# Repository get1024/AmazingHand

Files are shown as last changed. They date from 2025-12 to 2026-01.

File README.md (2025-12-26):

Project is licensed under [Apache 2.0](https://www.apache.org/licenses/LICENSE-2.0)

Mechanical design is licensed under a:
[Creative Commons Attribution 4.0 International License][cc-by].
[][cc-by]
[][cc-by]

[cc-by]: http://creativecommons.org/licenses/by/4.0/
[cc-by-image]: https://licensebuttons.net/l/by/4.0/88x31.png
[cc-by-shield]: https://img.shields.io/badge/License-CC%20BY-lightgrey.svg

# Amazing Hand project

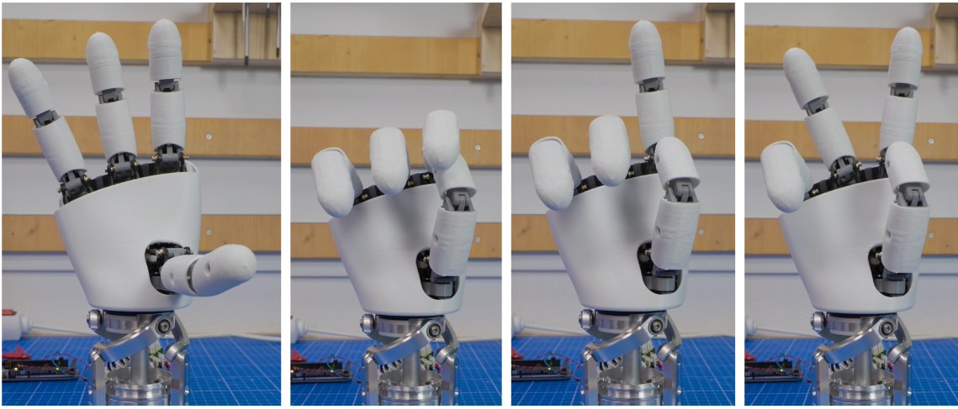
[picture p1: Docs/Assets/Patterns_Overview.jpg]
Patterns


Robotic hands are often very expensive and not so expressive. More dexterous ones often need cables and deported actuators in the forearm, i.e.,

The aim of this project is to be able to explore humanoid hand possibilities on a real robot (and Reachy2 is the perfect candidate for that !) with moderate cost.
=> Wrist interface is designed for Reachy2's wrist (Orbita 3D), but it can be easily adapted to other robot's wrist...

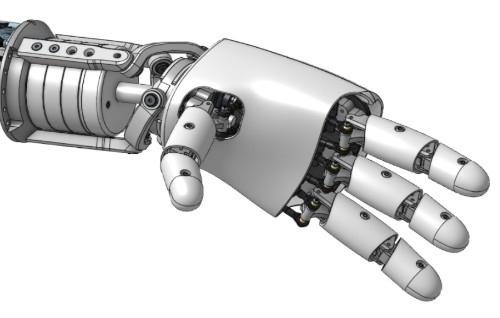
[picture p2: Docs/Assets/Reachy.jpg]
Reachy


Amazing Hand is:
- 8 dofs humanoid hand with 4 fingers
- 2 phalanxes per finger articulated together
- flexible shells almost everywhere
- All actuators inside the hand, without any cables
- 3D printable
- 400g weight
- low-cost (<200€)
- open-source

[AmazingHand_Overview](/docs/AmazingHand_Overview.pdf)

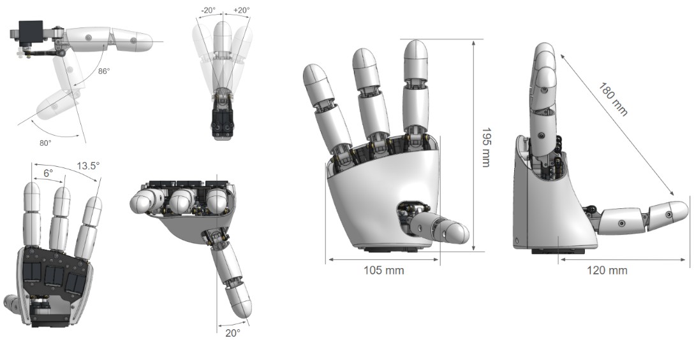
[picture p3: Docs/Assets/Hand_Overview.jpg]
Hand Overview

Each finger is driven by a parallel mechanism. 
That means 2x small Feetech SCS0009 servos are used to move each finger in flexion/extension and abduction/adduction

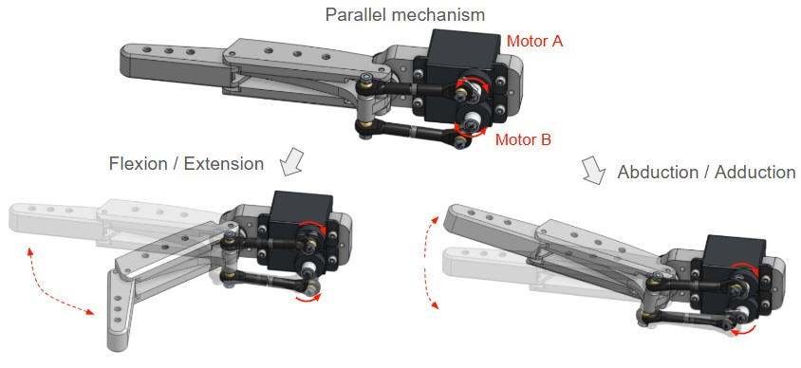
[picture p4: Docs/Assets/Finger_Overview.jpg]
Finger Overview


Two control methods are available:
- Use a serial bus driver (Waveshare i.e.) + Python script
- Use an Arduino + Feetech TTL Linker

Detailed explanations are available for both ways, and basic demo software is also available.
Up to you !

## Table of contents

- [Amazing Hand project](#amazing-hand-project)
  - [Table of contents](#table-of-contents)
- [Build Resources](#build-resources)
  - [BOM (Bill Of Materials)](#bom-bill-of-materials)
  - [CAD Files and Onshape document](#cad-files-and-onshape-document)
  - [Assembly Guide](#assembly-guide)
  - [Run basic Demo](#run-basic-demo)
  - [You need both right \& left hands on the same bus ?](#you-need-both-right--left-hands-on-the-same-bus-)
- [Disclaimer](#disclaimer)
- [AmazingHand advanced Demo](#amazinghand-advanced-demo)
- [Don't want to build it by yourself?](#dont-want-to-build-it-by-yourself)
- [Project Updates \& Community](#project-updates--community)
  - [Updates from community](#updates-from-community)
  - [To Do List](#to-do-list)
  - [FAQ](#faq)
  - [Contact](#contact)
  - [Thank you](#thank-you)

# Build Resources
## BOM (Bill Of Materials)
List of all needed components is available here:  
[AmazingHand BOM](https://docs.google.com/spreadsheets/d/1QH2ePseqXjAhkWdS9oBYAcHPrxaxkSRCgM_kOK0m52E/edit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)  
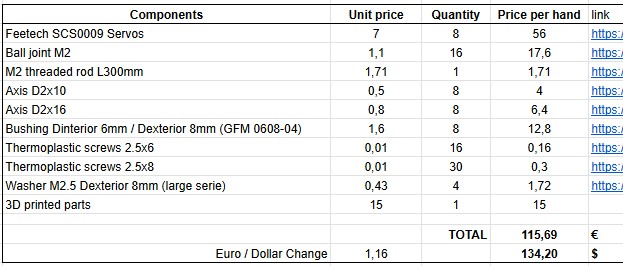
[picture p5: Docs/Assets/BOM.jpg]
BOM


And remember to add control choice cost (2 options detailed previously)

Details for custom 3D printed parts are here: 
[3Dprinted parts](https://docs.google.com/spreadsheets/d/1QH2ePseqXjAhkWdS9oBYAcHPrxaxkSRCgM_kOK0m52E/edit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)

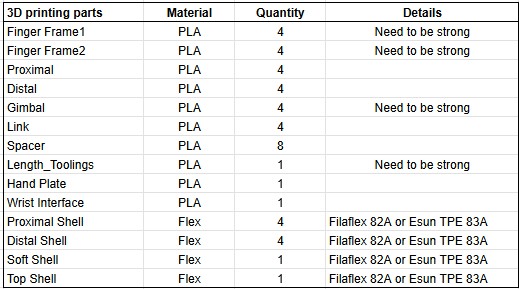
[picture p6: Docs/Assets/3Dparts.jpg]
3Dparts


Here is a guide explaining how to print all the needed custom parts:
[=> 3D Printing Guide](/docs/AmazingHand_3DprintingTips.pdf)
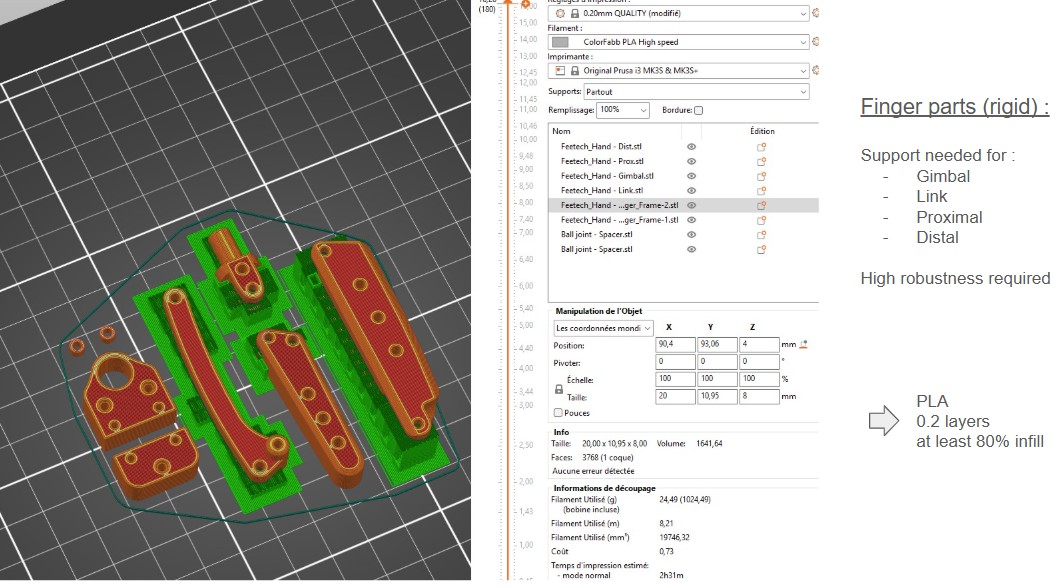
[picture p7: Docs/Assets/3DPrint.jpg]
3DPrint_example
 

## CAD Files and Onshape document
STL and Steps files can be found [here](https://github.com/pollen-robotics/AmazingHand/tree/main/cad) 

Note that fingers are the same if you want to build a left hand, but some parts are symmetrical. Specific right hand parts are preceded by an "R", and other left hand parts by an "L".

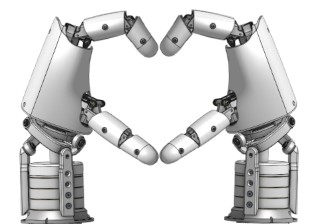
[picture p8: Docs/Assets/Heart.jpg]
Heart


Everyone can access the Onshape document too:   
[Link Onshape](https://cad.onshape.com/documents/430ff184cf3dd9557aaff2be/w/e3658b7152c139971d22c688/e/bd399bf1860732c6c6a2ee45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)  

Note that predefined positions are available in the "named position" tooling, with corresponding servo angles

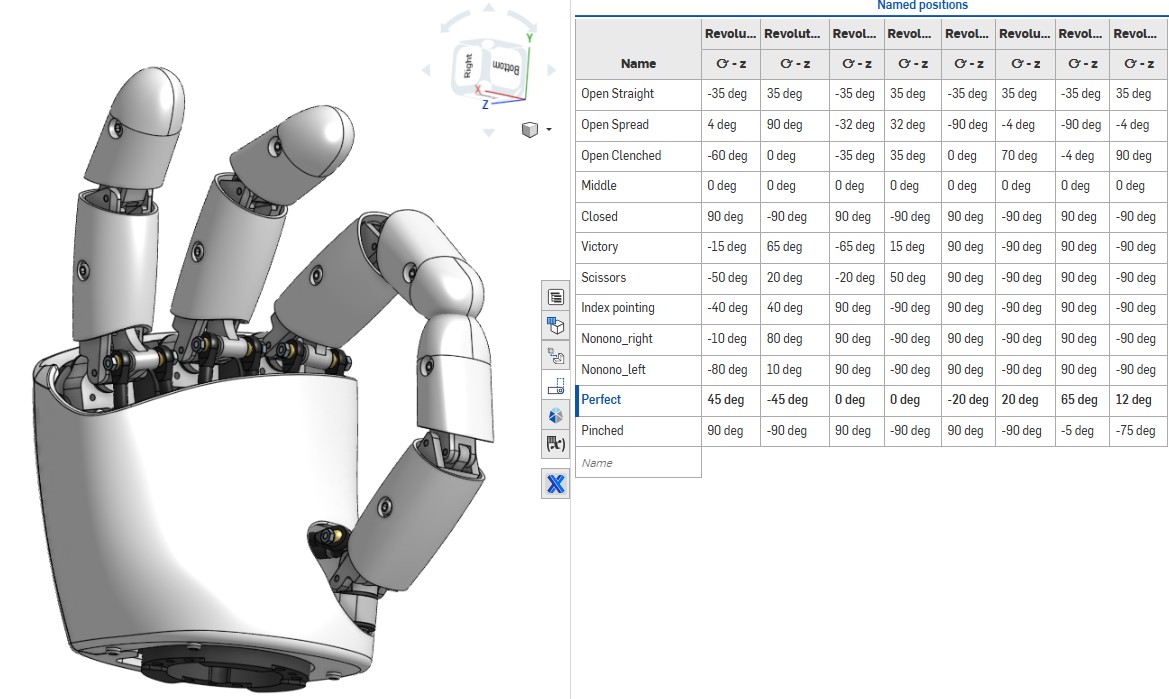
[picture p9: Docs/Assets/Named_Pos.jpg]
Onshape&Named_Pos
  

## Assembly Guide

Assembly guide for the Amazing Hand in combination with standard components in the BOM is here:  
[=> Assembly Guide](/docs/AmazingHand_Assembly.pdf)  
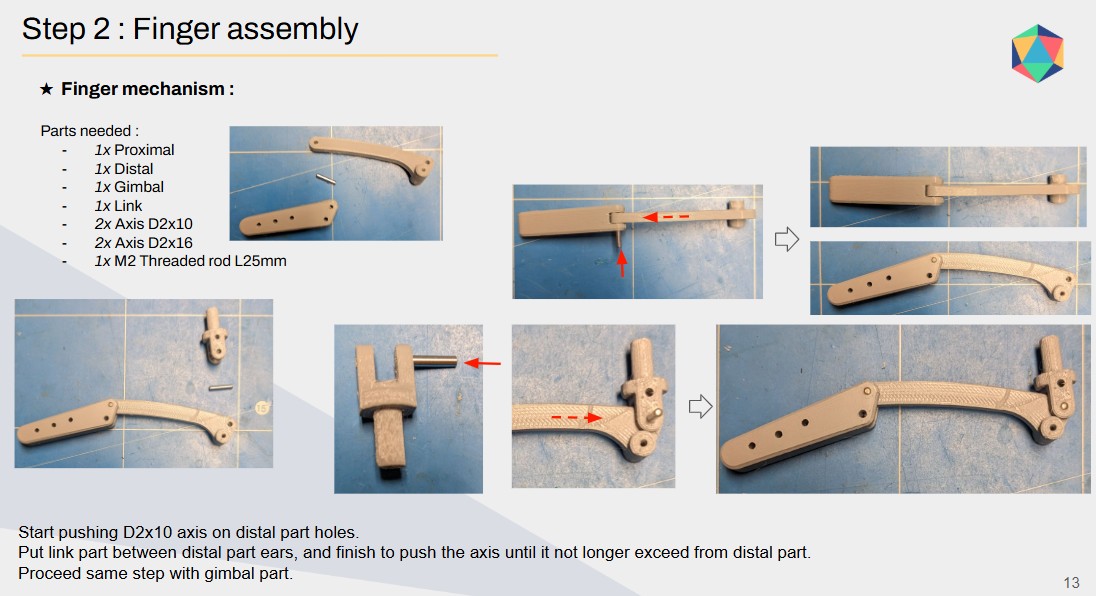
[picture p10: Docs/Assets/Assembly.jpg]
Assembly_example
  

You will need a simple program / script to calibrate each finger, available here:
- With Python & Waveshare serial bus driver: [here](https://github.com/pollen-robotics/AmazingHand/tree/main/PythonExample)
- With Arduino & TTLinker: [here](https://github.com/pollen-robotics/AmazingHand/tree/main/ArduinoExample)

Note that this assembly guide is for a standalone right hand.

If you need to build a standalone left hand, you can keep the same IDs for servo locations, and select if it's a right or left hand in the software.

## Run basic Demo

A basic demo is available with both Python & Arduino.

You will need an external power supply to be able to power the 8 actuators inside the hand.

If you don't have one already, a simple external power supply could be a DC/DC 220V -> 5V / 2A adapter with jack connector.
Check on the BOM list:
[AmazingHand BOM](https://docs.google.com/spreadsheets/d/1QH2ePseqXjAhkWdS9oBYAcHPrxaxkSRCgM_kOK0m52E/edit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) 

- Python script: "AmazingHand_Demo.py" [here](https://github.com/pollen-robotics/AmazingHand/tree/main/ArduinoExample)
  
- Arduino program: "AmazingHand_Demo.ino" [here](https://github.com/pollen-robotics/AmazingHand/tree/main/PythonExample)

https://github.com/user-attachments/Docs/Assets/485fc1f4-cc57-4e59-90b5-e84518b9fed0

## You need both right & left hands on the same bus ?

If you need to build both right and left hands to plug them on a robot, you will have to attribute different IDs for right and left hands. You can't have same ID for different servos on the same serial bus...
Very important thing is to keep same assembly order for servos, but set them different IDs than for the right hand, as follows:
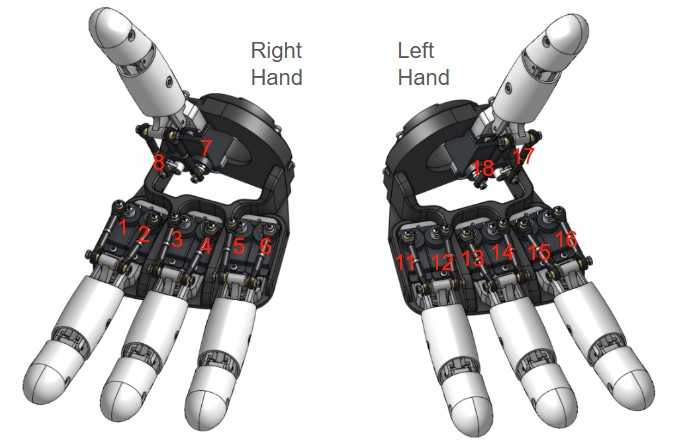
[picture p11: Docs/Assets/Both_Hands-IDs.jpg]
IDs


Specific software is also needed, in order to drive each hand independently.
This simple demo runs the same hand patterns on both hands simultaneously, but it's only available in Python:
"AmazingHand_Demo_Both" [here](https://github.com/pollen-robotics/AmazingHand/tree/main/PythonExample)

# Disclaimer

I noticed some variations between theoretical angles for Flexion / Extension, Abduction / Adduction and angles in real life prototypes. This is probably due to several sources of variation (3D printed parts are not perfect, balljoint rods are manually adjusted one by one, servo horn rework, flexibility of plastic parts...).

This design has not yet been tested for long and complex prehensile tasks. Before being able to grasp objects safely (that means without damaging servos or mechanical parts), a kind of smart software needs to be built.
SCS0009 servos have smart capabilities as:
- Torque enable / disable
- Torque feedback
- Current position sensor
- Heat temperature feedback
- ...

# AmazingHand advanced Demo
Tracking demo (https://www.youtube.com/watch?v=U0TfeG3ZUto)

For more advanced usage using inverse/forward kinematics there are several examples in the [Demo](Demo) directory along with some useful tools to test/configure the motors.

# Don't want to build it by yourself?
=> Kits are available here :

Seeed Studio :
https://www.seeedstudio.com/Amazing-Hand-Right-Hand-The-Open-Source-Robotic-Hand-Developer-Kit.html

WowRobo :
https://shop.wowrobo.com/products/amazing-hand-the-open-source-robotic-hand-kit

# Project Updates & Community
## Updates from community

- ### Amazing Base for the amazing hand : 
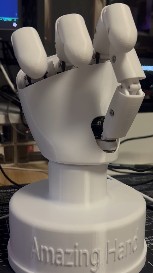
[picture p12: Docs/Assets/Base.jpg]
Base

STL or Step file can be found [here](https://github.com/pollen-robotics/AmazingHand/tree/main/cad) 

- ### Specific Chinese BOM available here :
[Chinese BOM](https://docs.google.com/spreadsheets/d/1fHZiTky79vyZwICj5UGP2c_RiuLLm89K8HrB3vpb2h4/edit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)

Thanks to Jianliang Shen !

- ### Amazing hand with SG90 servos + force control setup 🔥

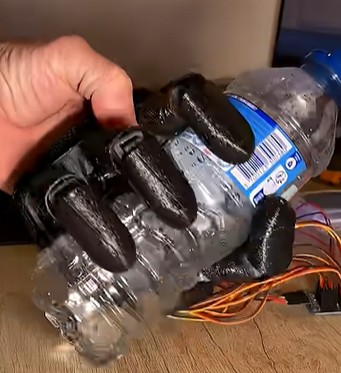
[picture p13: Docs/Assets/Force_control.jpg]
Force_control

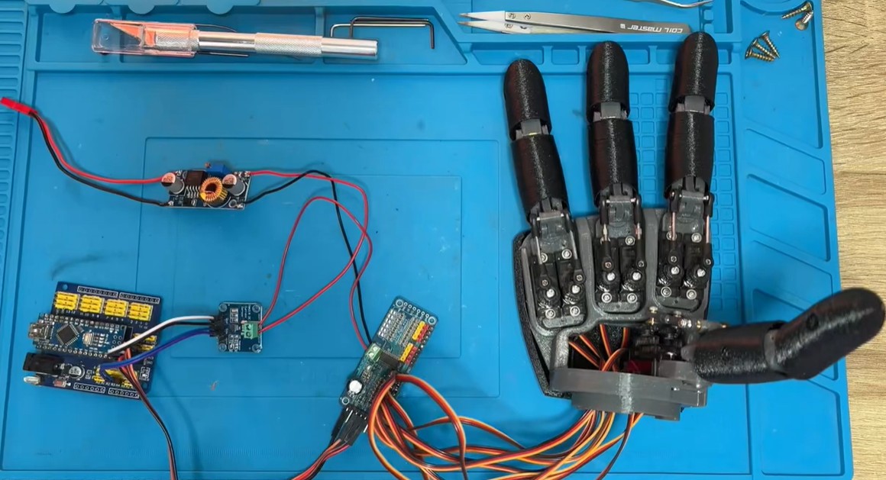
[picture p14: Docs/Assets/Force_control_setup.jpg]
Force_control_setup


GitHub with code: (https://github.com/joanbox24/AmazingHand-with-sg90-servo-force-control)

## To Do List
- Design small custom pcb with serial hub and power supply functions, to fit everything in the hand
- Test with prehensile tasks 
      => Add smarter behaviour for closing hand, based on available motors feedbacks
- Study possibility to have 4 different fingers length, or add a 5th finger
- Study possibility to use STS3032 Feetech motors instead of SCS0009
      => Stronger for quite the same volume, but servo horn is different
- Study possibility to add compliancy by replacing rigid links to springs
- Add fingertip sensor to push one step higher smart control

## FAQ
WIP

## Contact

You can reach public discord channel here : 
[Discord AmazingHand](https://discord.com/channels/519098054377340948/1395021147346698300)

Or 
[Contact me or Pollen Robotics](/docs/contact.md)

## Thank you
Huge thanks to those who have contributed to this project so far:
- [Steve N'Guyen](https://github.com/SteveNguyen) for beta testing, Feetech motors integration in Rustypot, Mujoco/Mink and hand tracking demo
- [Pierre Rouanet](https://github.com/pierre-rouanet) for Feetech motors integration in pypot  
- [Augustin Crampette](https://fr.linkedin.com/in/augustin-crampette) & [Matthieu Lapeyre](https://www.linkedin.com/in/matthieulapeyre/) for open discussions and mechanical advices

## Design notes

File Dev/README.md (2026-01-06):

# AmazingHand 控制实例教程

## 1. 知识大纲

`Dev` 目录包含以下核心组件：

*   **AHControl/**：基于 Rust 的驱动程序和机械手控制逻辑。
    *   `config/`：用于舵机映射和校准的 TOML 配置文件。
    *   `src/bin/`：用于舵机管理的实用二进制文件（`change_id`, `goto`, `get_zeros`, `set_zeros`）。
    *   `src/main.rs`：**Dora-rs** 管道的主控制节点。它读取 TOML 配置，监听来自仿真的关节位置更新（例如 `mj_r_joints_pos`），应用配置的偏移/反转，并同步写入舵机。
*   **AHSimulation/**：基于 MuJoCo 的物理仿真和逆运动学 (IK) 解算器。
    *   `Src/`：运行仿真的 Python 脚本（`mj_mink_right.py`）。
    *   `mjcf/`：手部的 XML 模型文件和 STL 资源。
    *   `examples/`：示例脚本（例如 `finger_angle_control.py`）。
*   **HandTracking/**：使用 MediaPipe 追踪人手动作的计算机视觉模块。
    *   `Src/main.py`：捕捉网络摄像头输入并输出手部关键点的主追踪节点。
*   **example/**：用于测试的独立示例。
    *   `PythonExample/`：直接控制舵机的 Python 脚本（不经过完整的 Dora 管道）。
    *   `ArduinoExample/`：用于底层测试的 Arduino 程序。
*   **数据流文件 (`*.yml`)**：**Dora-rs** 数据流的配置文件，定义了追踪、仿真和控制节点如何通信。

## 2. 使用方法

### 2.1 安装 C++生成工具 和 Windows 10/11 SDK

去 [Visual Studio](https://visualstudio.microsoft.com/zh-hans/) 官方下载 `Visual Studio Installer`

下载完成后双击  `VisualStudioInstaller.exe` 程序，选择 C++ 生成工具、Windows 10/11 SDK；

### 2.2 安装 Rust

去 [Rust](https://www.rust-lang.org/tools/install) 官网，点击 `Install Rust`

等待一段时间，你会得到 `rustup-init.exe`，先不着急双击运行。为了保证快速安装，先配置下载源。

编辑或新建文件：

```bash
C:\Users\<你的用户名>\.rustup\settings.toml
```

内容改成 / 确保包含：

```toml
default_toolchain = "stable-x86_64-pc-windows-msvc"

[dist]
server = "https://mirrors.tuna.tsinghua.edu.cn/rustup"
```

没有这个文件就自己新建，UTF-8 保存即可。

双击运行 `rustup-init.exe`，你会看到一个命令行窗口，内容大概是：

```sh
Welcome to Rust!

1) Proceed with installation (default)
2) Customize installation
3) Cancel installation
> 
```

直接按 `Enter` 键即可。等待一段时间，看到下述内容即安装完成：

```sh
Rust is installed now. Great!
```

重启终端，`VSCode`、`Trae`、`Cursor` 等编辑器也需要重启。在终端中依次输入：

```sh
rustc --version
cargo --version
```

看到版本信息就是安装成功了。

### 2.3 安装 Conda

[Conda 官方](https://www.anaconda.com/download)

### 2.4 安装 dora-rs

[dora-rs 官方](https://dora-rs.ai/docs/guides/Installation/installing)

```bash
cargo install dora-cli --locked
```

### 2.5 运行 Python 示例

创建环境并激活

```sh
conda create -n AmazingHand python=3.12.0
conda activate AmazingHand
```

安装依赖

```sh
pip install rustypot numpy opencv-python pillow pyserial mediapipe==0.10.14
```

运行演示脚本

```sh
python ./FixedAction/Python/AmazingHand_Demo.py
```

### 2.6 运行 Rust 示例

您可以使用 `AHControl` 中的 Rust 二进制文件调试单个舵机。在 `Dev` 目录下运行这些命令：

**移动单个舵机：**

```bash
cargo run --bin goto -- --id 1 --pos 0.5
```

- `--id`: 舵机 ID (1-8)。
- `--pos`: 目标位置，单位为弧度（大约 -1.5 到 1.5，取决于限制）。0.0 是配置的零位。

**修改舵机 ID：**

```bash
cargo run --bin change_id -- --old_id 1 --new_id 9
```

- 如果您更换了舵机并需要为其分配正确的 ID，这很有用。

**将手设置为零位：**

```bash
cargo run --bin set_zeros
```

- 将所有舵机移动到 `r_hand.toml` 中定义的偏移量位置。

**获取零位偏移量（校准）：**

```bash
cargo run --bin get_zeros
```

- 将舵机设置为柔顺模式并打印当前位置。

### 2.7 运行 HandTrackinig 示例

位于 `Dev/HandTracking`，该模块使用 **Google MediaPipe** 从网络摄像头源检测手部关键点。它被设计为一个 **Dora** 节点，向其他模块发布手部位置数据。

我们需要为 `HandTracking` (视觉) 和 `AHSimulation` (IK解算) 安装依赖。

在项目根目录 (`Dev/`) 下，通过 pip 安装这两个模块（以编辑模式安装，方便调试）：

```bash
# 激活你的 Python 虚拟环境
# 安装 HandTracking 依赖
pip install -e HandTracking

# 安装 AHSimulation 依赖
pip install -e AHSimulation
```

> **注意**: `AHSimulation` 依赖 `mujoco` 和 `mink`，安装时可能会下载较大的二进制文件，请保持网络通畅。

一切准备就绪后，启动 Dora 数据流：

**启动 Dora 守护进程 (Daemon)**:
打开一个新的终端：
```bash
dora up
```

**启动数据流**:
打开另一个终端，在 `Dev` 目录下运行：

- 仅在仿真环境中运行摄像头手部追踪演示程序：
  
```bash
dora build dataflow_tracking_simu.yml
dora run dataflow_tracking_simu.yml
```

- 要在真实硬件上运行摄像头手部追踪演示程序：

```bash
dora build dataflow_tracking_real.yml
dora run dataflow_tracking_real.yml
```

- 要在仿真环境中运行简单的示例来控制手指角度：

```bash
dora build dataflow_angle_simu.yml
dora run dataflow_angle_simu.yml
```

## 3. 手部配置

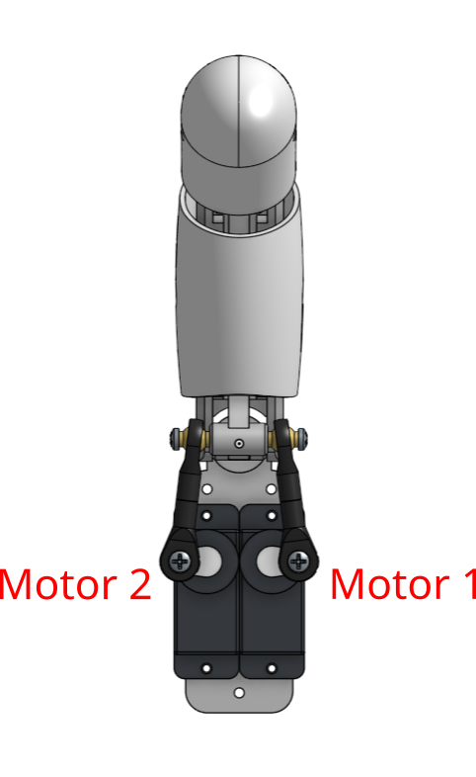
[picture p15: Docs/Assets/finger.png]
Motors naming Motors naming for each finger
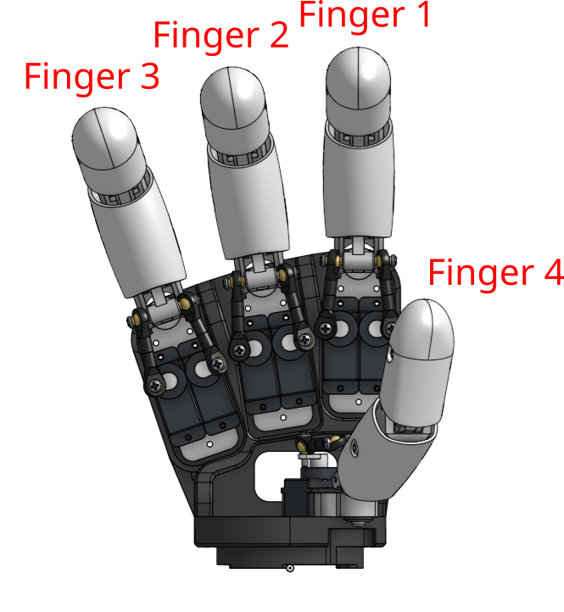
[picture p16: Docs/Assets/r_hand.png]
Fingers naming Fingers naming for each hand
|  |  |
|:-:|:-:|
| **_手指的舵机名称_** | **_每个手指的名称_** |

- 请务必根据你的实际手部设备，适配配置文件 [r_hand.toml](AHControl/config/r_hand.toml);
- 你可以使用 [AHControl](AHControl) 文件夹内的软件工具完成配置。

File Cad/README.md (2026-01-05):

Before print custom mechanical parts, please refer to 3D printing guide here :
在打印自定义机械部件之前，请参考3D打印指南：







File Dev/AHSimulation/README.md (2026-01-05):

# 基于MuJoCo的手部仿真

本项目包含 MuJoCo 仿真模型及资源文件，同时提供一个用于构建逆运动学求解问题的 Python 节点。

**[Mink](https://github.com/kevinzakka/mink)** 工具用于将逆运动学（IK）问题转化为二次规划（QP）问题进行求解。

用户可选择两种控制模式：一是指尖位置控制（pos）（适用于 **[手部追踪](../HandTracking/README.md)** 演示场景），二是远节指骨姿态控制（quat）。

AmazingHand 仿真模型由 CAD 文件导出，导出工具使用的是 **[onshape-to-robot](https://github.com/Rhoban/onshape-to-robot)**

# 文件说明与使用指南

## 1. 仿真节点 (**[Src/mj_mink_right.py](./Src/mj_mink_right.py)** / **[Src/mj_mink_left.py](./Src/mj_mink_left.py)**)

**功能**:
这两个文件分别对应右手和左手的 MuJoCo 仿真节点。它们使用 **[Mink](https://github.com/kevinzakka/mink)** 库来求解逆运动学 (IK)，根据输入的目标（位置或姿态）驱动仿真模型，并将计算出的关节角度输出。

**控制模式**:
- **`pos` (位置控制)**:
    - **描述**: 控制指尖在 3D 空间中的位置。
    - **适用场景**: 配合手部追踪 (**[HandTracking](../HandTracking/README.md)**) 使用，仿真手跟随真实手部动作。
    - **参数**: `lm_damping=0.05` (低阻尼，响应快，适合实时追踪，但是会产生一定的抖动，如果想要减少抖动，可以调高阻尼值)。
- **`quat` (姿态控制)**:
    - **描述**: 控制指尖的朝向 (四元数)。
    - **适用场景**: 精确角度控制测试 (如 **[finger_angle_control.py](./examples/finger_angle_control.py)**)。
    - **参数**: `lm_damping=1.0` (高阻尼，运动平滑稳定)。

**使用方法**:
通常作为 Dora 数据流的一部分运行，_**即不需要单独启动**_。
在 **[dataflow YAML 文件](../dataflow_tracking_real.yml)** 中配置：

```yaml
- id: hand_simulation
  build: pip install -e AHSimulation
  path: AHSimulation/Src/mj_mink_right.py
  inputs:
      hand_pos: hand_tracker/r_hand_pos
      tick: dora/timer/millis/2
      tick_ctrl: dora/timer/millis/10
  outputs:
      - mj_r_joints_pos
```

**运行结果**:
启动后会弹出一个 MuJoCo 被动查看器窗口，显示机械手的仿真模型。模型会根据输入数据实时运动。

## 2. 角度控制示例 (**[finger_angle_control.py](./examples/finger_angle_control.py)**)

**功能**:
这是一个测试节点，用于生成正弦波形式的手指角度控制信号 (四元数)。它演示了如何通过程序精确控制手指的弯曲和摆动。

**输出**:
`hand_quat`: 包含左右手各手指目标四元数的 PyArrow 数组。

**使用方法**:
配合 `quat` 模式的仿真节点使用。
在 dataflow YAML 文件中配置：
```yaml
- id: angle_control
  path: AHSimulation/examples/finger_angle_control.py
  inputs:
    tick: dora/timer/millis/20
  outputs:
    - hand_quat
```

**运行结果**:
仿真中的机械手手指会按照预定的正弦波规律不断弯曲和伸展。

## 3. 模型资源 (**[AH_Right/mjcf/](./Src/AH_Right/mjcf/)** & **[AH_Left/mjcf/](./Src/AH_Left/mjcf/)**)

**功能**:
包含机械手的 MuJoCo 模型定义文件 (`.xml`) 和 3D 网格文件 (`.stl`)。
- `scene.xml`: 定义了完整的仿真场景，包括光照、地面和机械手模型引用。
- `robot.xml`: 定义了机械手的物理属性、关节和传动关系。
- `assets/`: 存放所有零部件的 STL 模型文件。

**说明**:
这些文件通常不需要直接运行，而是被 Python 仿真节点加载。

## 4. 项目配置 (**[pyproject.toml](./pyproject.toml)**)

**功能**:
定义了 `AHSimulation` Python 包的元数据和依赖项。

**安装**:
在开发环境中安装此包：
```bash
pip install -e .
```

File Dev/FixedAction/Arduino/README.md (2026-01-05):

Feetech SCS0009 with Arduino tutorial :

[https://www.robot-maker.com/forum/topic/14804-presentation-et-fonctionnement-des-servomoteurs-feetech/]

Make sure to first install Arduino librairie "SCServo".

Install_SCServo_librairy Install SCServo with Arduino librairie manager

Use Feetech software to set IDs :
[https://github.com/Robot-Maker-SAS/FeetechServo/tree/main/feetech%20debug%20tool%20master/FD1.9.8.2)

# Summary in English (tutorial link is in french...)

## Wiring for link mode to change IDs of servos :

Upload Blink example program on arduino before opening serial port com with Feeetech software.

Link_Mode

Rx arduino pin connected to Tx pin on TTLinker / Tx arduino pin connected to Rx pin on TTLinker

## Wiring for control mode with arduino :

Upload custom program on arduino board.

Control_Mode

Rx arduino pin connected to Tx pin on TTLinker / Tx arduino pin connected to Rx pin on TTLinker

- For an arduino Uno (or other small arduinos with only one serial port), Serial communication setup need to be as follow :
Arduino_Uno_PortCom

- Note that Arduino used in this case is a Mega which have several serial ports embedded, so Serial communication setup need to be as follow :
Arduino_Mega_PortCom

Rx and Tx pin used on arduino Mega are RX1 & TX1 (19 & 18)

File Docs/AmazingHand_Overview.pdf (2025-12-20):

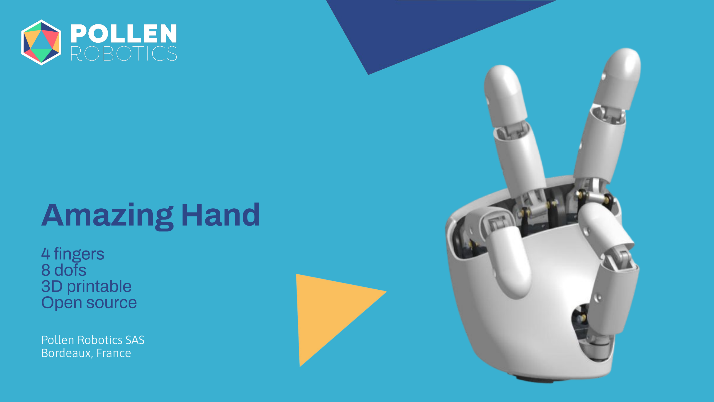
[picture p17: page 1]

Pollen Robotics SAS
Bordeaux, France

# Amazing Hand

### 4 fingers 8 dofs 3D printable Open source

## Amazing Hand

## Finger mechanism

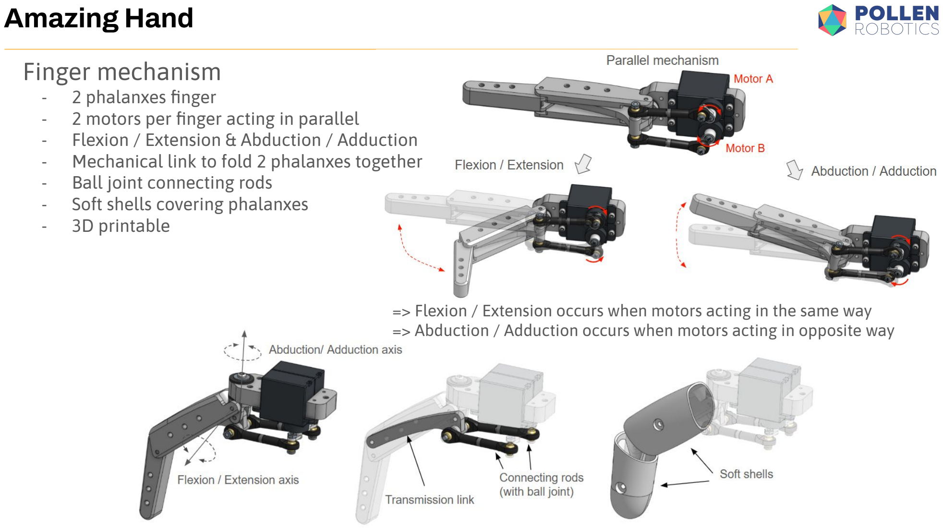
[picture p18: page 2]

- 2 phalanxes finger
- 2 motors per finger acting in parallel
- Flexion / Extension & Abduction / Adduction
- Mechanical link to fold 2 phalanxes together
- Ball joint connecting rods
- Soft shells covering phalanxes
- 3D printable

=> Flexion / Extension occurs when motors acting in the same way => Abduction / Adduction occurs when motors acting in opposite way

## Amazing Hand

## Hand design

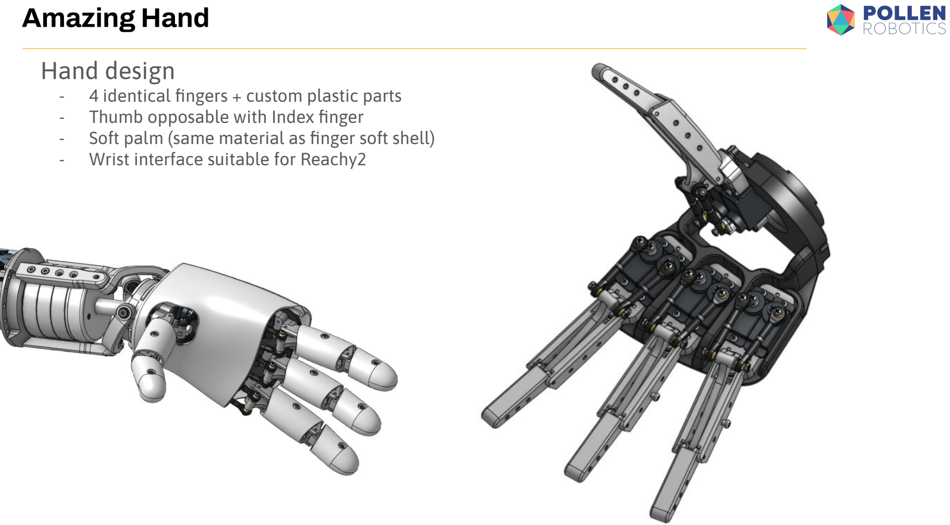
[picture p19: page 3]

- 4 identical fingers + custom plastic parts
- Thumb opposable with Index finger
- Soft palm (same material as finger soft shell)
- Wrist interface suitable for Reachy2

## Amazing Hand

## Technical details

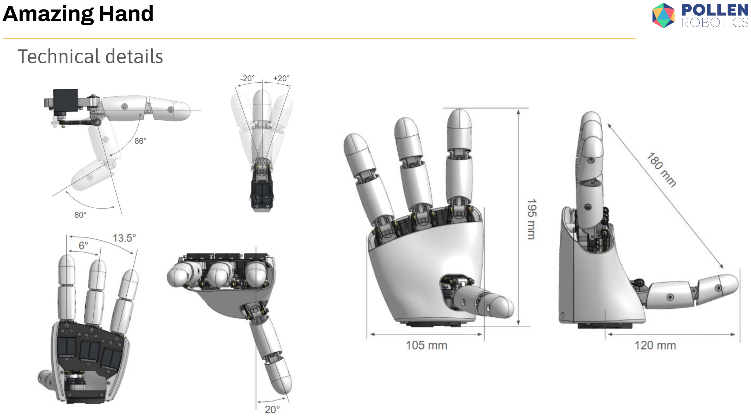
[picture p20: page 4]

## Amazing Hand

## Some of possible patterns

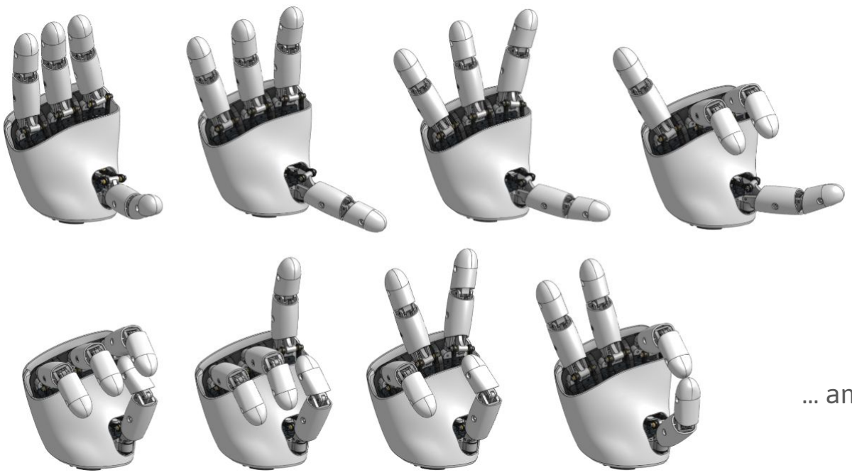
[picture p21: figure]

## … and others

## Amazing Hand

## Specifications

- x8 smart actuators (feetech SCS0009)
- DC Supply 5V / Max current 3A
- Weight : 400g
- Up to 1Kg payload
- 3D Printed suitable
- Fully open source (will be soon on github)
- Bom cost <200€ (assembly 5 - 6 hours)

It will be easy to :
- Add 5th finger (but will increase overall width)
- Size differently each finger
- Change position of fingers
- Add fingertip sensor (depends of which sensor obviously)
- Change wrist interface

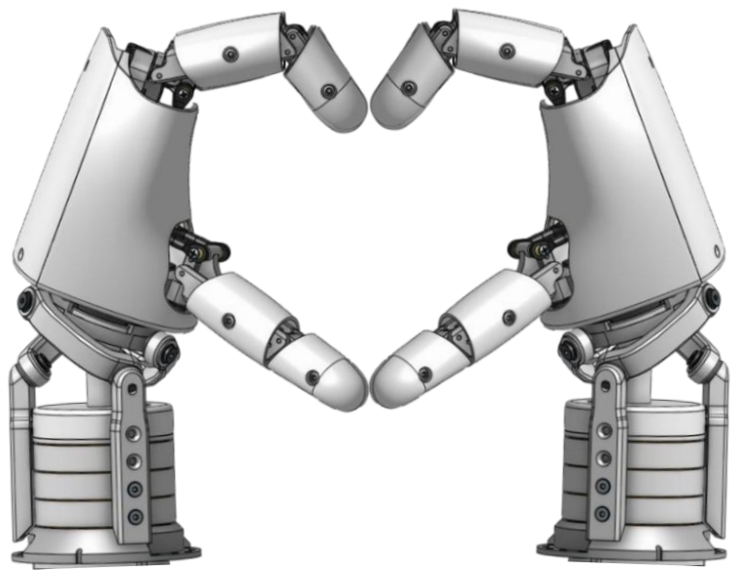
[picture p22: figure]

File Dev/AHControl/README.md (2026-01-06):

# 电机控制节点

电机配置在 TOML 文件中设置（参见 **[r_hand.toml](./config/r_hand.toml)**）。
在该文件中可以设置电机的 ID，以及每根手指的角度偏移。

- 使用 Feetech 软件设置 ID 及串行总线驱动教程：[https://www.robot-maker.com/forum/tutorials/article/168-brancher-et-controler-le-servomoteur-feetech-sts3032-360/]
- 通过 Feetech 软件设置 ID：[https://github.com/Robot-Maker-SAS/FeetechServo/tree/main/feetech%20debug%20tool%20master/FD1.9.8.2]、已经下载到 **[本地](../../../Tools/飞特舵机上位机软件/FD.exe)** 了

# 工具
- **[change_id](./src/bin/change_id.rs)**：帮助你更改电机的 ID。使用 `cargo run --bin=change_id -- -h` 查看参数列表
- **[goto](./src/bin/goto.rs)**：将单个电机移动到指定位置。使用 `cargo run --bin=goto -- -h` 查看参数列表
- **[get_zeros](./src/bin/get_zeros.rs)**：帮助设置电机零位，它会将电机置于柔顺模式并把 TOML 配置输出到控制台。使用 `cargo run --bin=get_zeros -- -h` 查看参数列表
- **[set_zeros](./src/bin/set_zeros.rs)**：根据配置文件将机械手移动到“零位”。使用 `cargo run --bin=set_zeros -- -h` 查看参数列表

# 入口文件
- **[main](./src/main.rs)**：程序的入口文件，包含初始化和主循环。它是一个 Dora 数据流节点，主要负责连接 Dora 框架 （接收指令）和 真实的机械手硬件 （发送控制信号）。

## 核心功能分析
1. 硬件初始化 ：
   - 读取配置文件（如 **[r_hand.toml](./config/r_hand.toml)** ），解析机械手的手指、电机 ID 和偏移量等信息。
   - 初始化串口通信（默认 COM3 ，波特率 1M），连接 Feetech SCS0009 舵机控制器。
   - 启动时开启电机扭矩，并根据配置将电机移动到初始位置。
2. Dora 数据流循环 ：
   - 初始化 Dora 节点，监听输入事件。
   - 接收数据 ：监听 `mj_l_joints_pos` 或 `mj_r_joints_pos` 输入（通常来自仿真节点）。这些数据是归一化的关节角度（Float64Array）。
   - 数据转换 ：将接收到的关节角度加上配置文件中定义的偏移量 ( offset )，并处理反向逻辑 ( invert )，计算出每个舵机的目标位置。
   - 控制执行 ：使用 `sync_write_goal_position` 指令，一次性同步写入所有舵机的目标位置，驱动机械手运动。
3. 退出处理 ：
   - 接收到 Stop 事件时，关闭电机扭矩并退出程序。

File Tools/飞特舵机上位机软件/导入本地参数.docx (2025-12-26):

导入本地参数

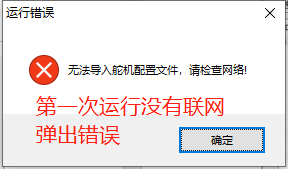
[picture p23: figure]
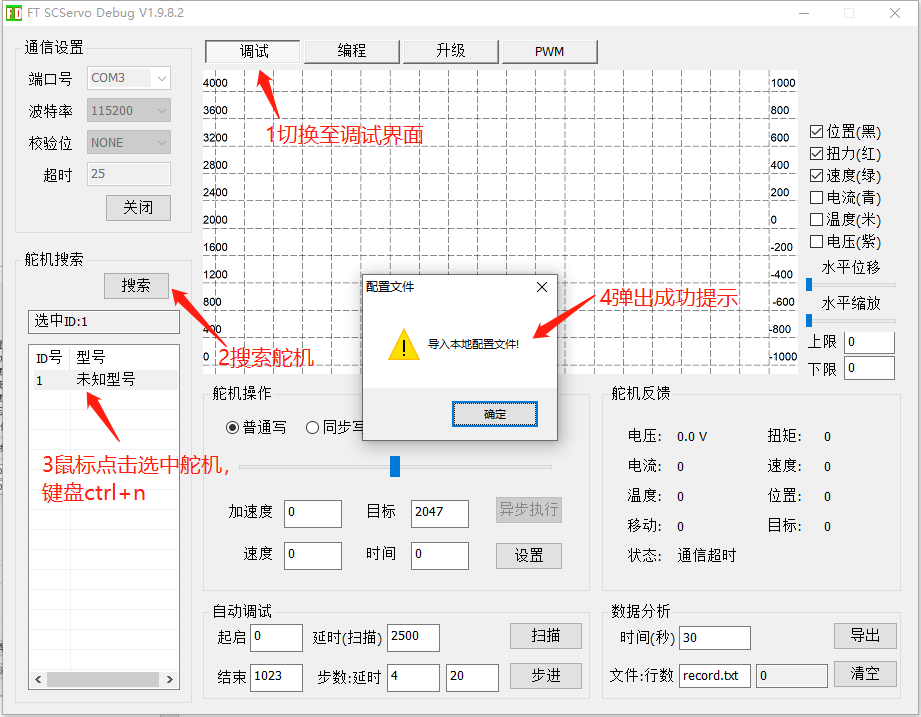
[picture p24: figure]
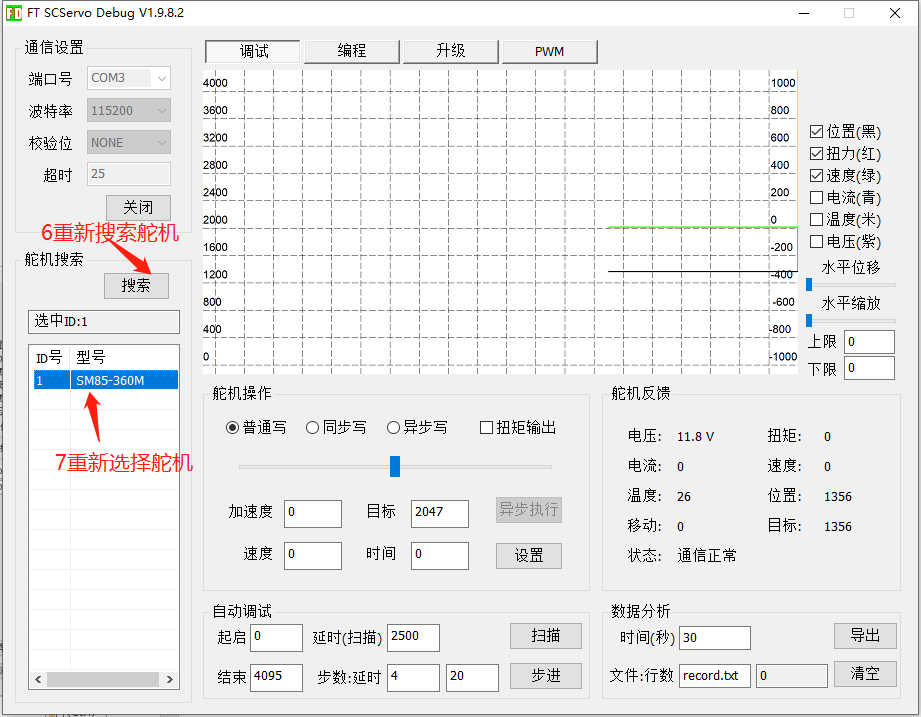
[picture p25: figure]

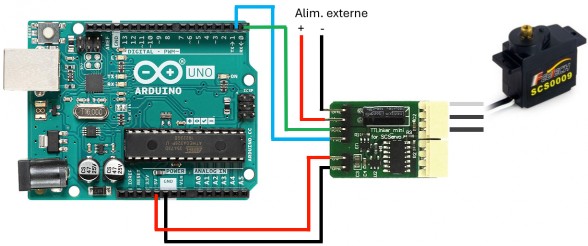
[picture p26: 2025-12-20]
Docs/Assets/Arduino_Control-mode.jpg

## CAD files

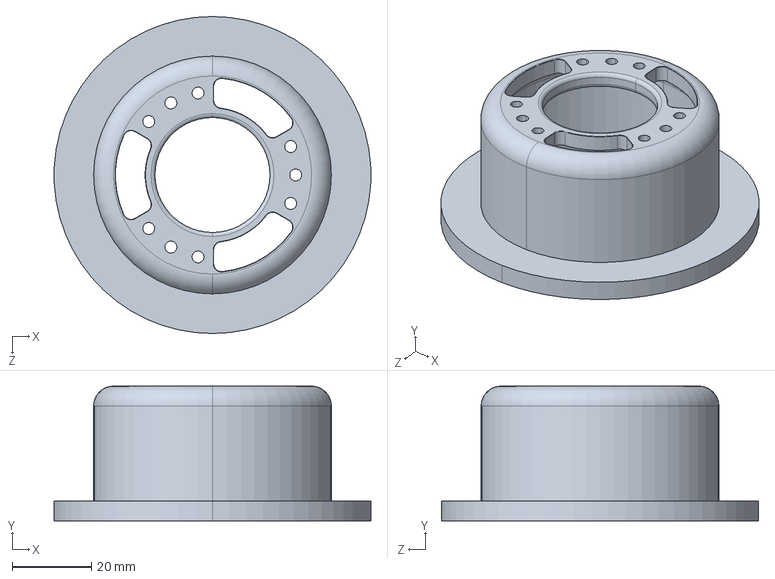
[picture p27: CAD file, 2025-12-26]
Cad/LeftHand/015base-1个.STEP
79.9 x 34.0 x 80.0 mm

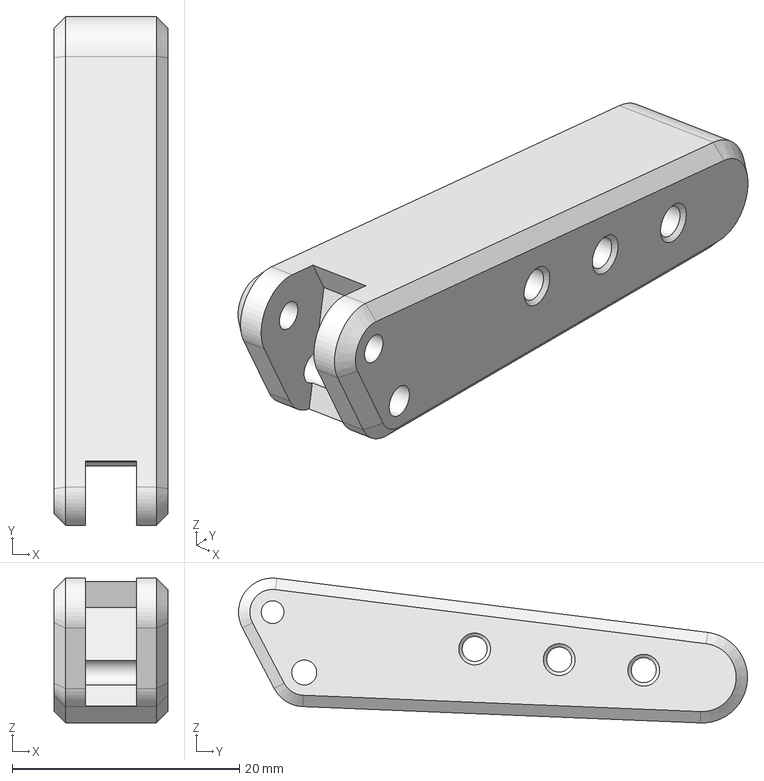
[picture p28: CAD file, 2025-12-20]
Cad/step/Amazing Hand Parts - Distal.step
10.0 x 44.8 x 12.8 mm

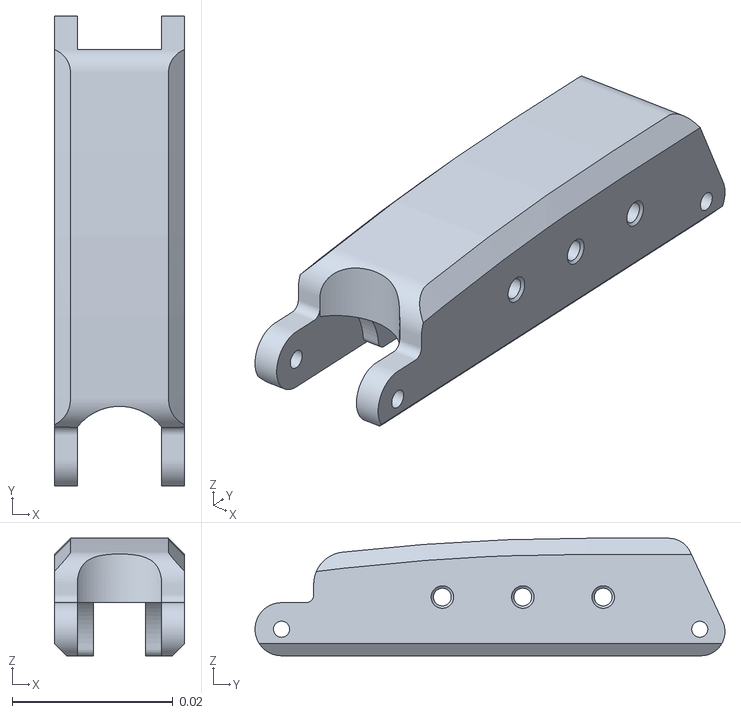
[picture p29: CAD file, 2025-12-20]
Dev/AHSimulation/Src/AH_Left/mjcf/assets/proximal.stl
0.0162 x 0.0584 x 0.0146

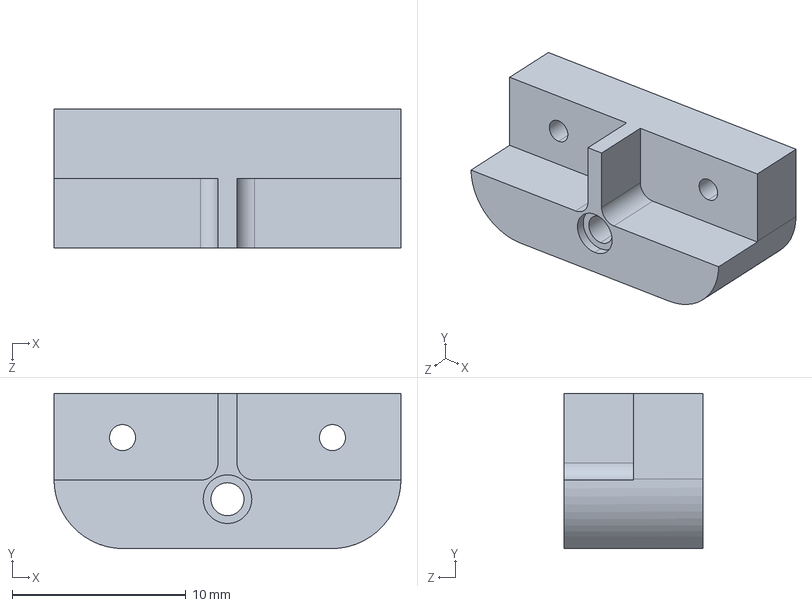
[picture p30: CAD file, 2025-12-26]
Cad/LeftHand/002finger_frame-2-3个-下沉.STEP
20.0 x 8.95 x 8.00 mm

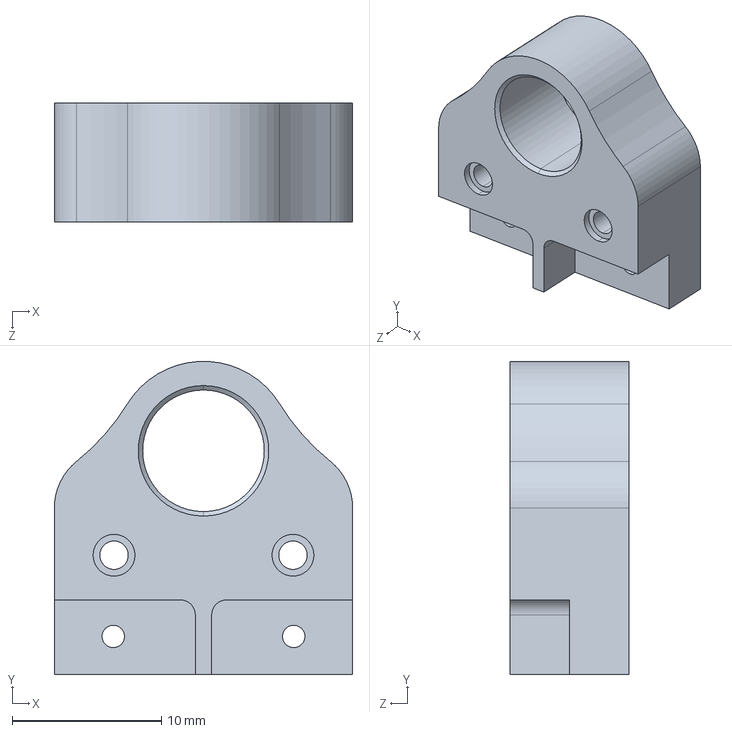
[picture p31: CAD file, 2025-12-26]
Cad/RightHand/001finger_frame-1-3个-下沉.STEP
20.0 x 21.0 x 8.00 mm

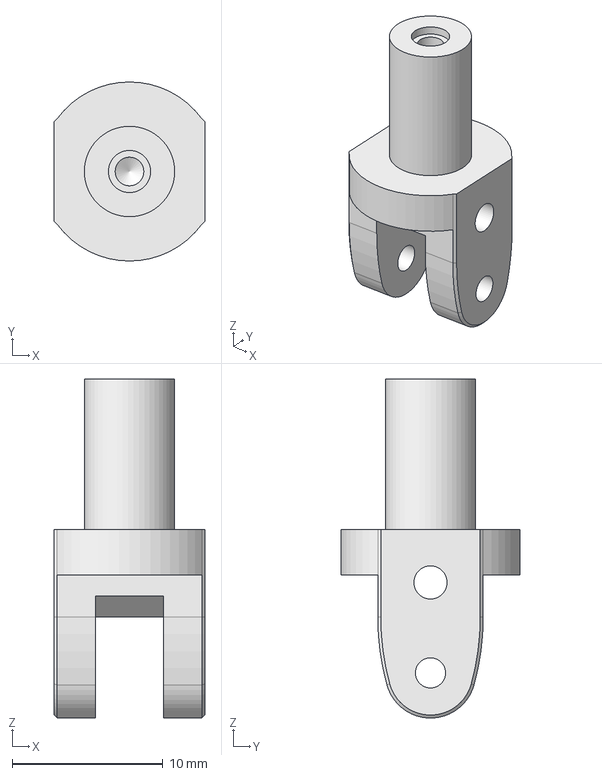
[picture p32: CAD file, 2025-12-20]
Cad/step/Amazing Hand Parts - Gimbal.step
10.0 x 11.9 x 22.5 mm

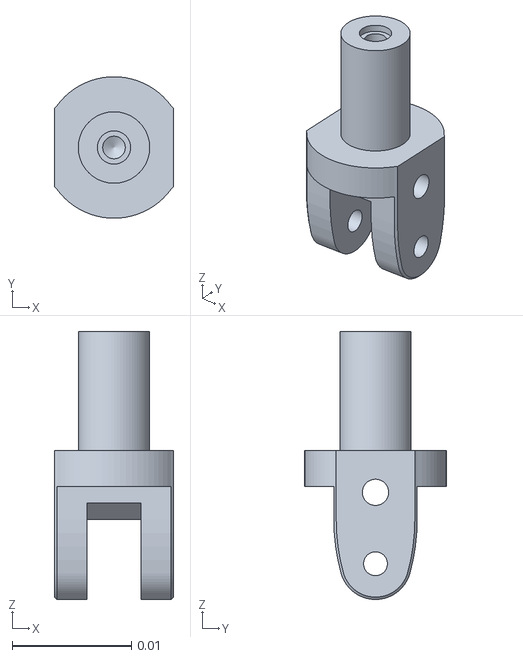
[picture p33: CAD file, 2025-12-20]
Dev/AHSimulation/Src/AH_Left/mjcf/assets/gimbal.stl
0.01 x 0.0119 x 0.0225

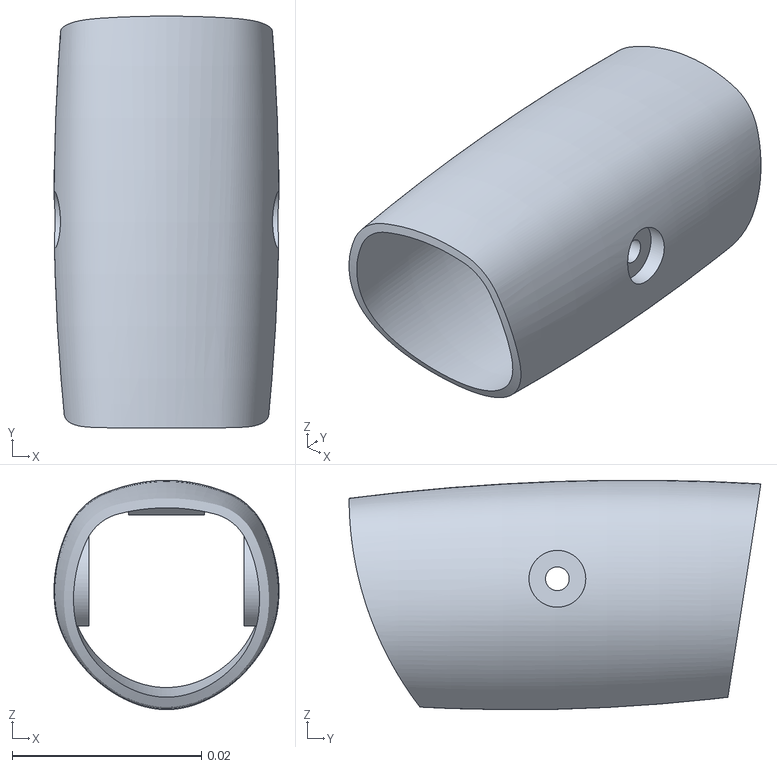
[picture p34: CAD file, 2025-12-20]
Dev/AHSimulation/Src/AH_Right/mjcf/assets/proximal_shell.stl
0.0238 x 0.0435 x 0.0242

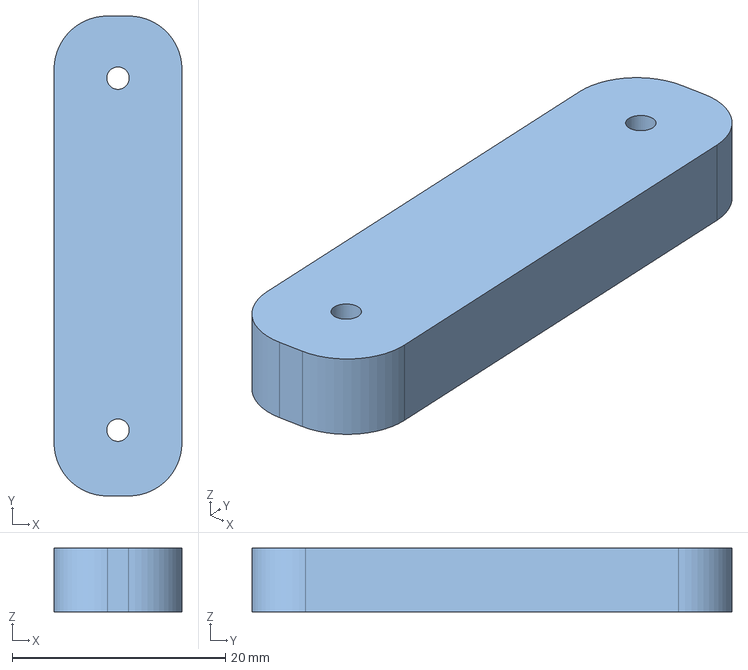
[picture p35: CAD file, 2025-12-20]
Cad/step/BallJoint_Rod - Length_Toolings.step
12.0 x 45.0 x 6.00 mm

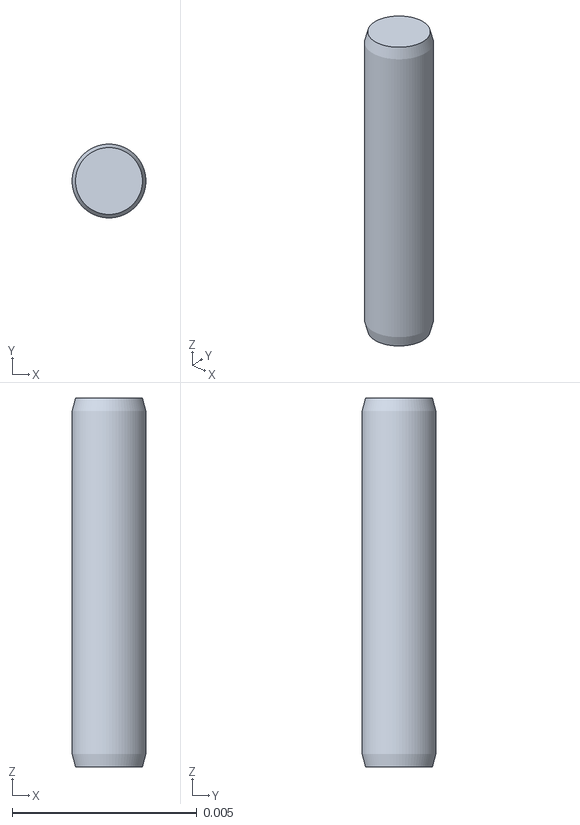
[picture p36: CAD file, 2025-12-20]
Dev/AHSimulation/Src/AH_Left/mjcf/assets/parallel_pin_2_x_10__fee063fca0c8b40e46bbc4ffff61d999.stl
0.002 x 0.002 x 0.01

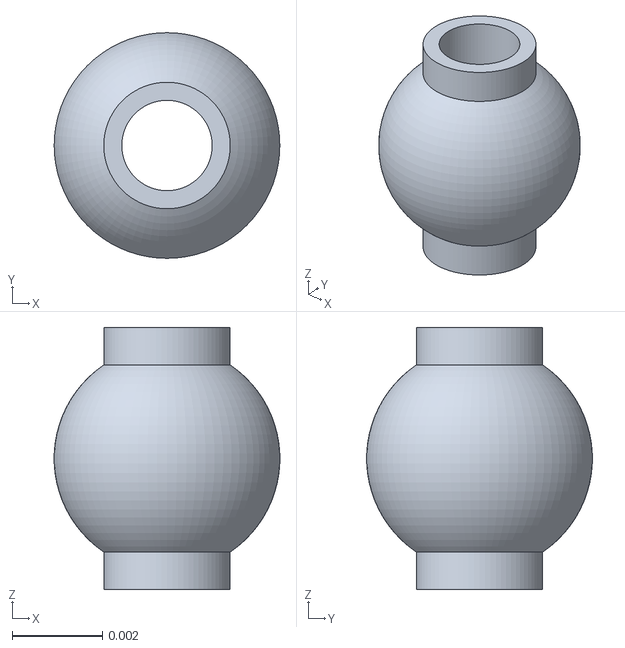
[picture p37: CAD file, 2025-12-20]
Dev/AHSimulation/Src/AH_Right/mjcf/assets/rotule_ball.stl
0.005 x 0.005 x 0.0058

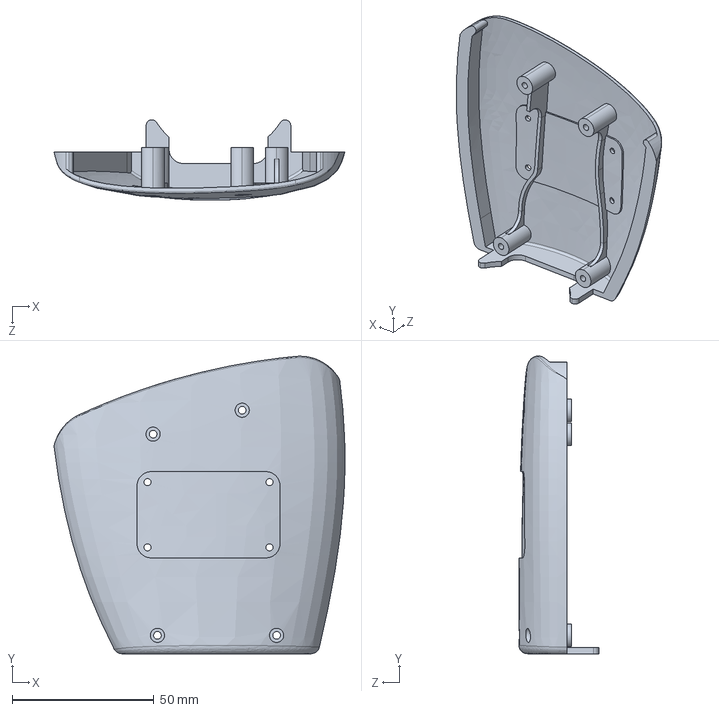
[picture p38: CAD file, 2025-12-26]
Cad/LeftHand/014L-top_shell软料1个.STEP
102.6 x 104.9 x 28.3 mm

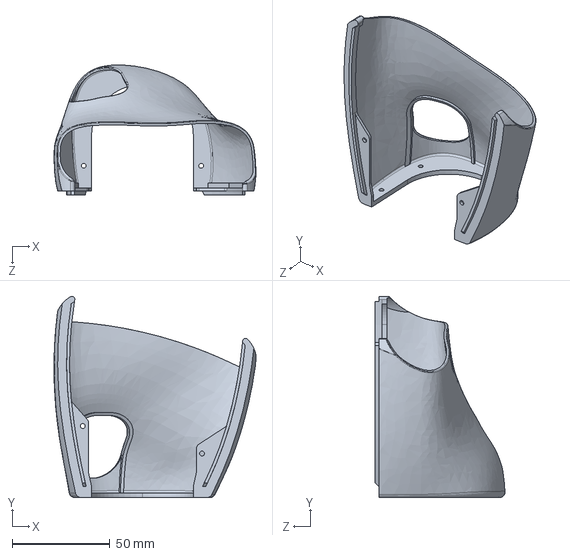
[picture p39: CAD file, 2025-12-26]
Cad/RightHand/013R-soft_shell-软料1个.STEP
103.2 x 102.9 x 66.4 mm

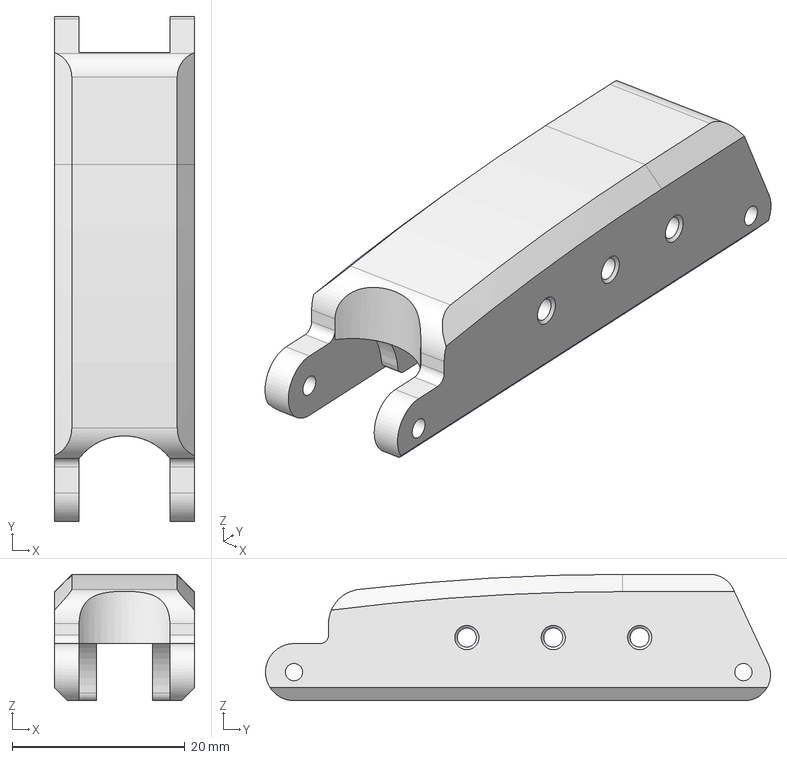
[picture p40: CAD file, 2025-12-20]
Cad/step/Amazing Hand Parts - Proximal.step
16.2 x 58.4 x 14.6 mm

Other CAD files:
Dev/AHSimulation/Src/AH_Left/mjcf/assets/finger_frame_2.stl
Cad/LeftHand/001Finger_Frame-1-1个.step
Cad/LeftHand/002Finger_Frame-2-1个.step
Cad/LeftHand/006Link-4个.step
Cad/LeftHand/007Spacer-8个.step
Cad/LeftHand/009L-Hand_Plate-1个.step
Cad/LeftHand/010L-Wrist_Interface-1个.step
Cad/LeftHand/011Proximal_Shell软料-4个.step
Cad/LeftHand/012Distal_Shell软料-4个.step
Cad/LeftHand/013L-soft_shell-软料1个.STEP
Cad/RightHand/001Finger_Frame-1-1个.step
Cad/RightHand/002Finger_Frame-2-1个.step
Cad/RightHand/006Link-4个.step
Cad/RightHand/007Spacer-8个.step
Cad/RightHand/009R-Hand_Plate-1个.step
Cad/RightHand/010R-Wrist_Interface-1个.step
Cad/RightHand/011Proximal_Shell软料-4个.step
Cad/RightHand/012Distal_Shell软料-4个.step
Cad/RightHand/014R-top_shell软料1个.STEP
Cad/step/Amazing Hand Parts - Distal_Shell.step
Cad/step/Amazing Hand Parts - Finger_Frame-1.step
Cad/step/Amazing Hand Parts - Finger_Frame-2.step
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

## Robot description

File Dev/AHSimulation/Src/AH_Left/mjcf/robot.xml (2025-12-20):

<?xml version="1.0" ?>
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
<mujoco model="mjcf">
  <compiler angle="radian" meshdir="assets" autolimits="true"/>
  <default>
    <default class="mjcf">
      <joint frictionloss="0.1" armature="0.005"/>
      <position kp="50" dampratio="1"/>
      <default class="visual">
        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
      </default>
      <default class="collision">
        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
      </default>
    </default>
  </default>
  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
  <default>
    <default class="perfect_actuator">
      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
      <joint damping="0.095" frictionloss="0.001" armature="0.001" range="-1.5707963267948966 1.5707963267948966"/>
      <position kp="10.0" kv="0.0" forcerange="-10.0 10.0"/>
      <default class="chosen_actuator"/>
    </default>
    <default class="xc330m288t">
      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
      <joint damping="0.095" frictionloss="0.058" armature="0.0018"/>
      <position kp="2.54" kv="0.0" forcerange="-0.8 0.8"/>
    </default>
    <default class="sts3215_345">
      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
      <joint damping="0.56" frictionloss="0.068" armature="0.027"/>
      <position kp="17.11" kv="0.0" forcerange="-3.23 3.23"/>
    </default>
    <default class="sts3215_147">
      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
      <joint damping="0.1" frictionloss="0.028" armature="0.011"/>
      <position kp="17.11" kv="0.0" forcerange="-1.35 1.35"/>
    </default>
  </default>
  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
  <default>
    <equality solref="0.002 1" solimp="0.99 0.999 0.0005 0.5 2"/>
  </default>
  <worldbody>
    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
    <body name="l_wrist_interface" pos="0 0 0" quat="1 0 0 0" childclass="mjcf">
      <inertial pos="0 0 0" mass="1e-09" fullinertia="1e-09 1e-09 1e-09 0 0 0"/>
      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
      <body name="custom_servo_horn" pos="-0.00755 -0.01845 0.0698" quat="0.5 0.5 -0.5 -0.5">
        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
        <joint axis="0 0 1" name="finger1_motor1" type="hinge" range="-1.5707963267680816 1.5707963268217116"/>
        <inertial pos="-0.005 1.45507e-17 -0.00655938" mass="0.000410988" fullinertia="4.63584e-09 4.63584e-09 1e-09 -5.13695e-25 5.13695e-25 -1.47358e-24"/>
        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
        <body name="ball_link" pos="-0.005 6.93889e-17 -0.0069" quat="0.00510149 -0.888984 0.0544589 0.454661">
          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
          <joint axis="0 0 1" name="passive_ball1" type="ball"/>
          <inertial pos="-1.373e-13 -0.0165 -1.373e-13" mass="0.000463323" fullinertia="6.40121e-08 1.59688e-09 6.40121e-08 6.6602e-19 -4.97671e-14 -6.66028e-19"/>
          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
          <body name="rotule_ball" pos="-5.09575e-18 -0.033 0" quat="0.707107 0 -0.707107 1.26027e-16">
            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
            <joint axis="0 0 1" name="passive_ball2" type="ball"/>
            <inertial pos="-0.0054579 -0.0141744 -0.00370248" mass="0.00277119" fullinertia="7.66485e-07 1.05617e-07 7.96842e-07 1.1411e-07 -1.27899e-08 -3.77417e-08"/>
            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
            <body name="std00333_plast_tcb_torx_2_5x8__configuration_copy_of_default" pos="-0.0116897 -0.000368272 -0.00081146" quat="0.778258 -0.271383 0.369077 -0.429475">
              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
              <joint axis="0 0 1" name="passive2 (1)" type="hinge"/>
              <inertial pos="-0.00530874 -0.00868244 0.00225" mass="0.00201325" fullinertia="9.34482e-08 4.69015e-08 1.16807e-07 -4.54529e-08 -5.39352e-21 1.85294e-21"/>
              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
            </body>
            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
            <body name="parallel_pin_2_x_10__fee063fca0c8b40e46bbc4ffff61d999" pos="0.00373407 -0.0482013 -0.00704062" quat="0.271383 0.778258 -0.429475 -0.369077">
              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
              <joint axis="0 0 1" name="passive4 (1)" type="hinge"/>
              <inertial pos="0.014571 -0.0133924 0.00225" mass="0.00540375" fullinertia="3.60212e-07 5.51031e-07 7.69492e-07 3.36413e-07 4.59548e-20 6.21363e-20"/>
              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
              <body name="parallel_pin_2_x_16__da4b7ddbe9d803fe3fbc70f2e822b99b" pos="-0.000346366 -0.00598999 0.00655" quat="1.94185e-14 -0.999998 -0.00198164 -2.33228e-14">
                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
                <joint axis="0 0 1" name="passive_5 (1)" type="hinge"/>
                <inertial pos="-0.0249171 -0.00392936 0.0052354" mass="0.0101851" fullinertia="4.96149e-07 2.52849e-06 2.3577e-06 2.45138e-08 1.19032e-10 3.03943e-10"/>
                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
              </body>
            </body>
          </body>
        </body>
      </body>
      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
      <body name="rotule_ball_2" pos="-0.00755 -0.03055 0.0698" quat="0.5 -0.5 -0.5 0.5">
        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
        <joint axis="0 0 1" name="finger1_motor2" type="hinge" range="-1.570796326794806 1.5707963267949872"/>
        <inertial pos="-0.005 1.45507e-17 -0.00655938" mass="0.000410988" fullinertia="4.63584e-09 4.63584e-09 1e-09 -1.2178e-24 2.18088e-24 1.16352e-24"/>
        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
        <body name="m2_rod_l18" pos="-0.005 -1.52656e-16 -0.0069" quat="0.413519 -0.0282313 0.909382 0.0350781">
          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
          <joint axis="0 0 1" name="passive_ball3" type="ball"/>
          <inertial pos="-1.37294e-13 -0.0165 -1.37308e-13" mass="0.000463323" fullinertia="6.40121e-08 1.59688e-09 6.40121e-08 6.66049e-19 -4.97671e-14 -6.66038e-19"/>
          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
        </body>
      </body>
      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
      <body name="custom_servo_horn_2" pos="-0.00755 0.0109301 0.0632994" quat="0.525483 0.473147 -0.525483 -0.473147">
        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
        <joint axis="0 0 1" name="finger2_motor1" type="hinge" range="-1.5707963267948992 1.570796326794894"/>
        <inertial pos="-0.005 4.23062e-17 -0.00655938" mass="0.000410988" fullinertia="4.63584e-09 4.63584e-09 1e-09 -9.01595e-25 2.80049e-24 -1.33994e-24"/>
        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
        <body name="ball_link_2" pos="-0.005 4.16334e-17 -0.0069" quat="0.050917 0.0053796 0.0199815 0.998488">
          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
          <joint axis="0 0 1" name="passive_ball4" type="ball"/>
          <inertial pos="-1.37302e-13 -0.0165 -1.373e-13" mass="0.000463323" fullinertia="6.40121e-08 1.59688e-09 6.40121e-08 6.66029e-19 -4.97671e-14 -6.66029e-19"/>
          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
          <body name="rotule_ball_3" pos="-3.46945e-18 -0.033 -2.1684e-18" quat="0.707107 -4.70416e-17 -0.707107 -2.22045e-16">
            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
            <joint axis="0 0 1" name="passive_ball5" type="ball"/>
            <inertial pos="0.000263719 -0.0141744 0.00658995" mass="0.00277119" fullinertia="7.98353e-07 1.05617e-07 7.64973e-07 -9.81456e-08 -1.07431e-08 -6.93752e-08"/>
            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
            <body name="std00333_plast_tcb_torx_2_5x8__configuration_copy_of_default_2" pos="0.00629123 -0.000368272 0.00988571" quat="0.0211395 -0.505685 0.861078 0.0487841">
              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
              <joint axis="0 0 1" name="passive2 (2)" type="hinge"/>
              <inertial pos="-0.00530874 -0.00868244 0.00225" mass="0.00201325" fullinertia="9.34482e-08 4.69015e-08 1.16807e-07 -4.54529e-08 -3.42753e-22 -2.4785e-22"/>
              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
            </body>
            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
            <body name="parallel_pin_2_x_10__fee063fca0c8b40e46bbc4ffff61d999_2" pos="-0.00788193 -0.0482013 0.00117849" quat="0.505685 0.0211395 0.0487841 -0.861078">
              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
              <joint axis="0 0 1" name="passive4 (2)" type="hinge"/>
              <inertial pos="0.014571 -0.0133924 0.00225" mass="0.00540375" fullinertia="3.60212e-07 5.51031e-07 7.69492e-07 3.36413e-07 -3.71294e-22 -4.40498e-22"/>
              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
              <body name="parallel_pin_2_x_16__da4b7ddbe9d803fe3fbc70f2e822b99b_2" pos="-0.000346366 -0.00598999 0.00655" quat="2.91464e-16 0.999998 0.00198164 -1.68066e-16">
                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
                <joint axis="0 0 1" name="passive_5 (2)" type="hinge"/>
                <inertial pos="-0.0249171 -0.00392936 0.0052354" mass="0.0101851" fullinertia="4.96149e-07 2.52849e-06 2.3577e-06 2.45138e-08 1.19032e-10 3.03943e-10"/>
                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
              </body>
            </body>
          </body>
        </body>
      </body>
      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
      <body name="rotule_ball_4" pos="-0.00755 -0.00110358 0.0645642" quat="0.473147 -0.525483 -0.473147 0.525483">
        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
        <joint axis="0 0 1" name="finger2_motor2" type="hinge" range="-1.570796326794869 1.570796326794924"/>
        <inertial pos="-0.005 4.23062e-17 -0.00655938" mass="0.000410988" fullinertia="4.63584e-09 4.63584e-09 1e-09 -4.00354e-24 -8.99961e-24 7.94132e-24"/>
        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

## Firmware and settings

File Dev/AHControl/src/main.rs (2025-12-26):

use clap::Parser;
// use dora_node_api::{dora_core::config::NodeId, DoraNode, Event};

// use dora_node_api::IntoArrow;
use dora_node_api::{self, arrow::array::Array, DoraNode, Event, Parameter};
use eyre::{eyre, Result};
use rustypot::servo;
use std::{error::Error, time::Duration};

use facet::Facet;
use facet_pretty::FacetPretty;
// use std::{collections::HashMap, path::PathBuf, sync::Arc};
// use std::error::Error;
// use arrow_convert::{
//     deserialize::TryIntoCollection, serialize::TryIntoArrow, ArrowDeserialize, ArrowField,
//     ArrowSerialize,
// };
use std::{fs, thread};

// use std::io::Read;
#[derive(Debug, Facet)]
struct Fingers {
    #[allow(dead_code)] // Disable dead code warning for the entire struct
    motors: Vec<Motors>,
}

#[derive(Debug, Facet)]
struct Motors {
    #[allow(dead_code)] // Disable dead code warning for the entire struct
    finger_name: String,
    #[allow(dead_code)] // Disable dead code warning for the entire struct
    motor1: Motor,
    #[allow(dead_code)] // Disable dead code warning for the entire struct
    motor2: Motor,
}

#[derive(Debug, Facet)]
struct Motor {
    #[allow(dead_code)]
    id: u8,
    #[allow(dead_code)]
    offset: f64,
    #[allow(dead_code)]
    invert: bool,
    #[allow(dead_code)]
    model: String,
}

#[derive(Parser, Debug)]
#[command(author, version, about, long_about = None)]
struct Args {
    /// Serialport
    #[arg(short, long, default_value = "COM3")]
    serialport: String,
    /// baudrate
    #[arg(short, long, default_value_t = 1_000_000)]
    baudrate: u32,
    /// TOML config file
    #[arg(short, long, default_value = "config/r_hand.toml")]
    config: String,
}

fn main() -> Result<(), Box<dyn Error>> {
    let args = Args::parse();
    let serialport: String = args.serialport;
    let baudrate: u32 = args.baudrate;
    let configfile: String = args.config;
    println!("Opening {:?}", configfile);
    let toml_str = fs::read_to_string(configfile).expect("Failed to read config file");

    let motors_conf: Fingers =
        facet_toml::from_str(&toml_str).expect("Failed to deserialize config file");

    println!("{}", motors_conf.pretty());
    let serial_port = serialport::new(serialport, baudrate)
        .timeout(Duration::from_millis(10))
        .open()?;

    let mut controller = servo::feetech::scs0009::Scs0009Controller::new()
        .with_protocol_v1()
        .with_serial_port(serial_port);

    if motors_conf.motors[0].motor1.model != *"SCS0009" {
        return Err(eyre!("Only SCS0009 motors are supported for now...").into());
    };

    // let output = DataId::from("pull_position".to_owned());
    let mut finger_names: Vec<String> = vec![];
    let mut motor_ids: Vec<u8> = vec![];
    let mut motor_offsets: Vec<f64> = vec![];
    let motors = &motors_conf.motors;
    for motors in motors {
        finger_names.push(motors.finger_name.clone());
        motor_ids.push(motors.motor1.id);
        motor_ids.push(motors.motor2.id);
        motor_offsets.push(motors.motor1.offset);
        motor_offsets.push(motors.motor2.offset);
    }
    let motors_on: Vec<u8> = vec![1; motor_ids.len()];
    let motors_off: Vec<u8> = vec![0; motor_ids.len()];

    //torque enable
    controller.sync_write_torque_enable(&motor_ids, &motors_on)?;
    thread::sleep(Duration::from_millis(1000));
    controller.sync_write_goal_position(&motor_ids, &motor_offsets)?;
    thread::sleep(Duration::from_millis(1000));
    let (mut _node, mut events) =
        // DoraNode::init_from_node_id(NodeId::from("hand_controller".to_string()))?;
        DoraNode::init_from_env()?;

    let mut motors_ids: Vec<u8> = Vec::with_capacity(16);
    let mut motors_goalpos: Vec<f64> = Vec::with_capacity(16);

    while let Some(event) = events.recv() {
        match event {
            Event::Input { id, metadata, data } => match id.as_str() {
                "mj_l_joints_pos" | "mj_r_joints_pos" => {
                    let buffer: &dora_node_api::arrow::array::Float64Array =
                        data.as_any().downcast_ref().unwrap();
                    let buffer: &[f64] = buffer.values();
                    // println!("data: {:?}", buffer);

                    motors_ids.clear();
                    motors_goalpos.clear();

                    for (_idx, finger) in motors.iter().enumerate() {
                        // println!("conf: {:?} {:?}", idx, finger.finger_name);

                        if let Some(Parameter::ListInt(finger1_idx)) =
                            metadata.parameters.get(&finger.finger_name)
                        {
                            // println!(
                            //     "metadata: name: {:?} idx {:?} data: {:?} {:?}",
                            //     finger.finger_name,
                            //     finger1_idx,
                            //     buffer[finger1_idx[0] as usize],
                            //     buffer[finger1_idx[1] as usize]
                            // );
                            // controller.sync_write_goal_position(
                            //     &[finger.motor1.id, finger.motor2.id],
                            //     &[
                            //         buffer[finger1_idx[0] as usize] + finger.motor1.offset,
                            //         buffer[finger1_idx[1] as usize] + finger.motor2.offset,
                            //     ],
                            // )?;

                            motors_ids.push(finger.motor1.id);
                            motors_ids.push(finger.motor2.id);

                            let mut m1goal = buffer[finger1_idx[0] as usize] + finger.motor1.offset;
                            if finger.motor1.invert {
                                m1goal = -m1goal;
                            }
                            motors_goalpos.push(m1goal);
                            let mut m2goal = buffer[finger1_idx[1] as usize] + finger.motor2.offset;
                            if finger.motor2.invert {
                                m2goal = -m2goal;
                            }
                            motors_goalpos.push(m2goal);

                            // controller.write_goal_position(
                            //     finger.motor1.id,
                            //     buffer[finger1_idx[0] as usize] + finger.motor1.offset,
                            // )?;
                            // thread::sleep(Duration::from_millis(10));
                            // controller.write_goal_position(
                            //     finger.motor2.id,
                            //     buffer[finger1_idx[1] as usize] + finger.motor2.offset,
                            // )?;
                            // thread::sleep(Duration::from_millis(10));
                        }
                    }
                    controller.sync_write_goal_position(&motors_ids, &motors_goalpos)?;
                    // let parameters = MetadataParameters::default();
                    // let e: Vec<f64> = Vec::new(); //TODO return actual positions
                    // node.send_output(output.clone(), parameters, e.into_arrow())?;
                }
                other => println!("Received input `{other}`"),
            },
            Event::Stop(stop_cause) => {
                eprintln!("Received stop: {:?}", stop_cause);
                return Ok(());
            }
            _ => {}
        }
    }
    println!("Quitting");
    //torque off
    controller.sync_write_torque_enable(&motor_ids, &motors_off)?;
    thread::sleep(Duration::from_millis(1000));
    Ok(())
}

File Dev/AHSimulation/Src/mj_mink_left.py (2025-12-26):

"""Mujoco Client: This node is used to represent simulated robot, it can be used to read virtual positions, or can be controlled."""

import argparse

import os
import time

import mujoco
import mujoco.viewer
import pyarrow as pa
from dora import Node

import mink
from loop_rate_limiters import RateLimiter
from mink.contrib import TeleopMocap
from pathlib import Path
import numpy as np

ROOT_PATH = Path(os.path.dirname(os.path.abspath(__file__)))


class Client:
    """TODO: Add docstring."""

    def __init__(self, mode='pos'):
        """TODO: Add docstring."""


        self.model = mujoco.MjModel.from_xml_path(
            (ROOT_PATH / "AH_Left/mjcf/scene.xml").as_posix()
        )
        # self.data=mujoco.MjData(self.model)


        self.configuration = mink.Configuration(self.model)

        self.posture_task = mink.PostureTask(self.model, cost=1e-2)

        if mode=='pos':
            self.task1 = mink.FrameTask(
                frame_name='tip1',
                frame_type="site",
                position_cost=1.0,
                orientation_cost=0.0,
                lm_damping=1.0,
            )

            self.task2 = mink.FrameTask(
                frame_name='tip2',
                frame_type="site",
                position_cost=1.0,
                orientation_cost=0.0,
                lm_damping=1.0,
            )

            self.task3 = mink.FrameTask(
                frame_name='tip3',
                frame_type="site",
                position_cost=1.0,
                orientation_cost=0.0,
                lm_damping=1.0,
            )

            self.task4 = mink.FrameTask(
                frame_name='tip4',
                frame_type="site",
                position_cost=1.0,
                orientation_cost=0.0,
                lm_damping=1.0,
            )
        elif mode=='quat': #we control the orientation
            self.task1 = mink.FrameTask(
                frame_name='tip1',
                frame_type="site",
                position_cost=0.0,
                orientation_cost=1.0,
                lm_damping=1.0,
            )

            self.task2 = mink.FrameTask(
                frame_name='tip2',
                frame_type="site",
                position_cost=0.0,
                orientation_cost=1.0,
                lm_damping=1.0,
            )

            self.task3 = mink.FrameTask(
                frame_name='tip3',
                frame_type="site",
                position_cost=0.0,
                orientation_cost=1.0,
                lm_damping=1.0,
            )

            self.task4 = mink.FrameTask(
                frame_name='tip4',
                frame_type="site",
                position_cost=0.0,
                orientation_cost=1.0,
                lm_damping=1.0,
            )
        else:
            print(f"Error, unknown mode: {mode}")
            return -1
        # Regulate all equality constraints with the same cost.
        eq_task = mink.EqualityConstraintTask(self.model, cost=1000.0)

        self.tasks = [
            eq_task,
            self.posture_task,
            self.task1,
            self.task2,
            self.task3,
            self.task4,
        ]



        self.model = self.configuration.model
        self.data = self.configuration.data
        self.solver = "quadprog"

        self.motor_pos=[]
        self.metadata=[]
        self.node = Node()

    def run(self):
        """TODO: Add docstring."""
        with mujoco.viewer.launch_passive(self.model, self.data) as viewer:

            rate = RateLimiter(frequency=500.0)
            # dt = rate.dt
            # t = 0
            self.configuration.update_from_keyframe("zero")

            # Initialize mocap bodies at their respective sites.
            self.posture_task.set_target_from_configuration(self.configuration)

            mink.move_mocap_to_frame(self.model, self.data, "finger1_target", "tip1", "site")
            mink.move_mocap_to_frame(self.model, self.data, "finger2_target", "tip2", "site")
            mink.move_mocap_to_frame(self.model, self.data, "finger3_target", "tip3", "site")
            mink.move_mocap_to_frame(self.model, self.data, "finger4_target", "tip4", "site")


            for event in self.node:
                event_type = event["type"]

                if event_type == "INPUT":
                    event_id = event["id"]

                    if event_id == "tick":
                        # self.node.send_output("tick", pa.array([]), event["metadata"])

                        if not viewer.is_running():
                            break

                        step_start = time.time()



                        self.task1.set_target(
                            mink.SE3.from_mocap_name(self.model, self.data, "finger1_target")
                        )
                        self.task2.set_target(
                            mink.SE3.from_mocap_name(self.model, self.data, "finger2_target")
                        )
                        self.task3.set_target(
                            mink.SE3.from_mocap_name(self.model, self.data, "finger3_target")
                        )
                        self.task4.set_target(
                            mink.SE3.from_mocap_name(self.model, self.data, "finger4_target")
                        )





                        # vel = mink.solve_ik(self.configuration, self.tasks, self.model.opt.timestep, self.solver, 1e-5)
                        # self.configuration.integrate_inplace(vel, self.model.opt.timestep)
                        vel = mink.solve_ik(self.configuration, self.tasks, rate.dt, self.solver, 1e-5)
                        self.configuration.integrate_inplace(vel, rate.dt)



                        # Step the simulation forward
                        # mujoco.mj_step(self.m, self.data)

                        # mujoco.mj_step(self.model, self.data)


                        #get the motors position and send
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

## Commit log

2025-12-20 feat: 添加AmazingHand项目初始文件及文档
    添加项目文档、3D模型、示例代码和配置文件
    包括Python和Arduino示例、仿真控制节点、手部追踪节点
    添加CAD模型、组装指南和3D打印建议2025-12-16-19-53-RyanJoy
    [Amazing Hand Parts - Distal.step, Amazing Hand Parts - Distal.stl, Amazing Hand Parts - Distal_Shell.step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]
2025-12-20 chore: 从git中移除.DS_Store并更新.gitignore
    添加.DS_Store到.gitignore以避免未来提交
2025-12-20 feat(CVCursor): 实现虚拟鼠标核心功能与设计文档
    添加虚拟鼠标控制器实现，包含手部检测、坐标映射和鼠标事件处理
    重构设计文档结构并补充详细实现细节
2025-12-21 feat(鼠标控制): 添加Mac UI元素吸附功能并优化手势控制
    - 新增MacUiSnapper类实现界面元素吸附功能
    - 优化手势检测算法，增加锚点选择和捏合阈值控制
    - 改进光标移动平滑度和响应速度
    - 添加错误处理和调试信息
    - 修复mediapipe导入问题和摄像头权限提示
2025-12-22 chore: 在.gitignore中添加机械手材料目录
    忽略机械手材料目录以避免将其纳入版本控制
2025-12-26 feat: Add project resources, CAD models, and documentation; update code
    [001Finger_Frame-1-1个.step, 001finger_frame-1-3个-下沉.STEP, 002Finger_Frame-2-1个.step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]
2025-12-26 refactor: 优化代码结构和性能，修复路径问题
    - 统一将模块路径从 `AHSimulation/AHSimulation/` 改为 `AHSimulation/Src/`
    - 降低 Mujoco 仿真频率从 1000Hz 到 500Hz 以提高性能
    - 修复路径处理逻辑，使用正确的根路径
    - 优化 OpenCV 视频捕获缓冲区设置，减少延迟
    - 调整 IK 求解器阻尼参数，改善手部追踪响应
    - 优化 Rust 控制器的内存分配，重用向量缓冲区
    - 更新 YAML 配置文件中的路径和参数
    [main.rs, mj_mink_left.py, mj_mink_right.py]
2025-12-26 feat: 添加机器人手部控制演示GIF
    整理Arduino和Python版本的机器人手部控制代码所在文件夹
    添加演示视频转换的GIF文件和相关文档说明
2025-12-26 fix(AmazingHand_Demo): 修复主函数调用并添加手部动作测试
    将主函数调用改为直接测试手部开合动作
    添加1秒延迟确保动作完成
2025-12-27 docs(TestVlog): 添加手部追踪测试的演示gif文件
2026-01-05 docs(3D打印指南): 更新文档并替换为新的图片资源
    删除旧的PDF引导手册，整理为图片嵌入的markdown手册
2026-01-05 docs(AHControl): 更新README文档，完善工具和核心功能说明
    - 添加工具对应的源码文件链接
    - 补充入口文件和核心功能分析
    - 修正格式和重复内容
2026-01-05 docs(AHSimulation): 更新README文档为中文版本并补充使用说明
    更新项目文档为中文版本，详细说明仿真节点功能、控制模式及使用方法。
    新增文件结构说明和示例程序使用指南，便于开发者快速理解项目架构。
2026-01-05 chore: 移除废弃的AI虚拟鼠标项目代码和设计文档
2026-01-05 docs: 更新项目文档并删除冗余文件
    - 将README.md内容从英文翻译为中文并补充详细使用指南
    - 删除HandTracking/README.md和Docs/Info.md冗余文档
    - 更新FixedAction目录下的README.md文件内容
    - 优化文档结构，提供更清晰的中文使用说明
2026-01-06 feat(控制面板): 添加机械手控制GUI应用并优化核心类
    refactor: 将AmazingHand_Demo.py重构为AmazingHand_Demo_Optimized.py
    docs: 更新README文件路径并添加项目介绍文档
    style: 注释掉演示代码中的测试动作
2026-01-06 fix(AmazingHand): 修正中指移动参数以避免无效动作
    将Move_Middle方法的参数从(0, -0)改为(-35, 35)，避免执行无效的零移动操作
2026-01-08 refactor(GUI): 优化代码加载逻辑并添加重新加载功能
    移除AmazingHand_Demo_Optimized.py中的多余空行
    注释掉dataflow_tracking_simu.yml中未使用的模拟节点
    在HandControlApp中添加动态重新加载模块功能
    删除过时的intro.md文档

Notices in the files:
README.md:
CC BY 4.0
